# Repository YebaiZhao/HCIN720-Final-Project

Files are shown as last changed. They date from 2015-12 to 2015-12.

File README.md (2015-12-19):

# HCIN720-Final-Project
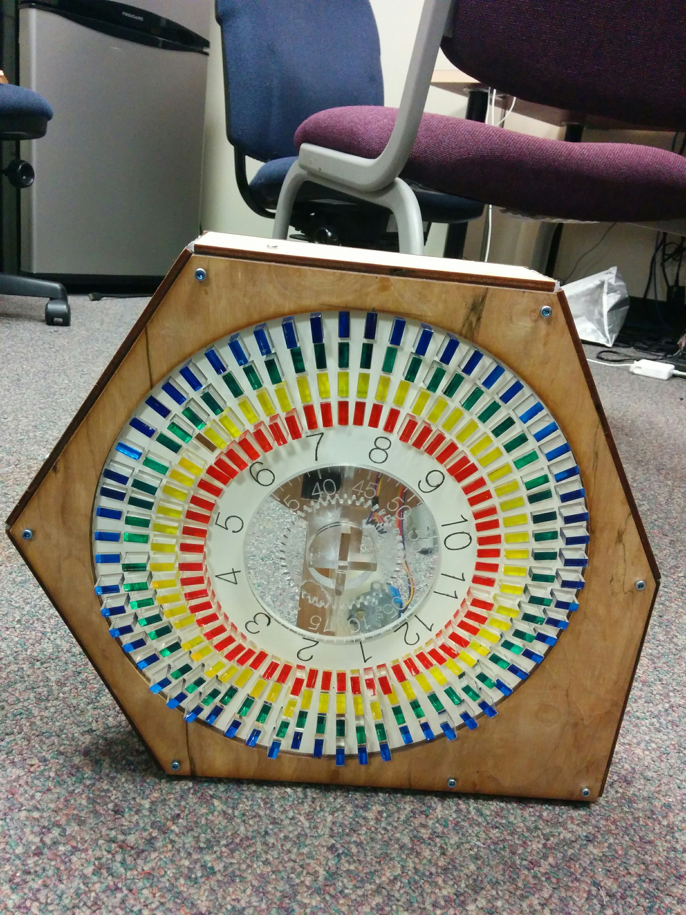
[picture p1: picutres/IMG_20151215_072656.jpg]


A complete prototype including Software for [Photon](https://store.particle.io/), 3D Model, Laser cutting Material for recreating. 

.... is a clock like device for recording the data-- like light temperature and motion, happend around house in 12 hours.

### Docs & Help

- [Software for Photon]() (latest release)
- [3D printing](/3D%20printing%20and%20CAD)
- [laser cutting](/Laser%20Cut)

### 3D printing part

3D printing parts are for holding the minute step motor and hour step motor, which rotate the gears. The .gcode file is avalible [here](/3D%20printing%20and%20CAD/final-motor_holder.gcode) for 3D printing. You could also check the model outlook [here](/3D%20printing%20and%20CAD/final-motor_holder.stl).

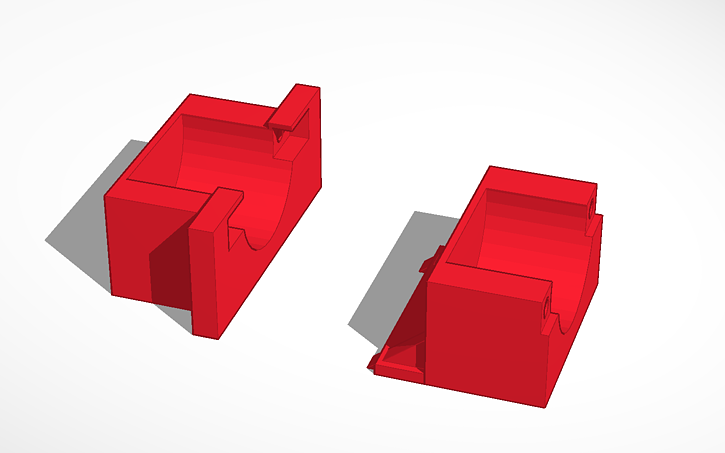
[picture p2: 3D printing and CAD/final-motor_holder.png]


### laser cutting

Laser cutting are serveral part, including, the hour plate, minute plate, gears, acrylic bricks, center support material and the outter box, servo holder. All the parts are avaliable in this [.ai file](/Laser%20Cut/v7.ai) at different layers. The final printing might look like this.

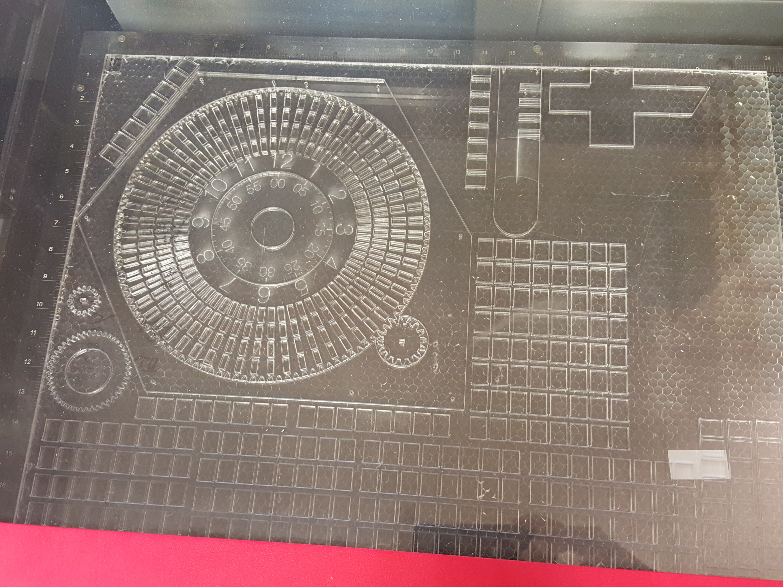
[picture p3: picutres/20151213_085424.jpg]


To customize your own clock, you could paint the hour plate, minute plate and acrylic bricks in different color. We printed the hour plate with white, and acrylic bricks with blue, red, green and yellow, like the first picture.

### Software installation

There are three different files in the software part. The .ino file are avaliable for two photon. [One](/Code/clockOperation.ino) take care of clock operation(including two [step motors](http://www.amazon.com/gp/product/B00JB22IQC?psc=1&redirect=true&ref_=oh_aui_detailpage_o09_s00) and two SG92 servo), and another [one](/Code/sensor.ino) for data collection(here we provide the light sensor and [motion sensor](http://www.amazon.com/gp/product/B013LA6MW0?psc=1&redirect=true&ref_=oh_aui_detailpage_o00_s00) code). Another [.html](/Code/test-version1.html) file is for get temperature data from [weather map API](http://openweathermap.org/api) and send it to photon.

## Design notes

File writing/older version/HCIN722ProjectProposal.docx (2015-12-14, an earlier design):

Project AirDrums

Project Idea and Motivation

Learning to play the drums can be very difficult for some people. They are expensive, with the cost for a complete drum kit ranging from $300-$1000, depending on quality, brand, usage and number of parts. They also require a large space for storage. And last of all, they are loud. Playing the drums can often bother neighbors, or even the residents that live in the same house. As an alternative, there are electronic drums that can solve the noise problem, but, although smaller than the standard drums, they’re hard to carry around.

By building a prototype for a virtual, mobile drum kit, this project aims at enabling its users to carry their “drums” around, wherever they go, requiring only a head-mounted display, some fiducial marker(s) and haptic drum sticks. The use of such a system will not only help aspiring drummers around the world to play and enjoy the music that they love, but also allow individuals to learn and practice, without the complications of purchasing and storing a physical drum kit.

Group Members & Roles

Names | Roles
Anthony Jimenez | Software Programming (good at C#, Python and Java).
Dhananjai Hariharan | Research, System Design, Software Programming (Java, C++, C#. Experience in Android App Development).
Shitao Guo | Software Programming (good at Java, Processing and a little bit C), and soldering if needed.
Tiago Justino | Software Programming (experience with embedded systems and Android. Experience with C, C++, Java, Ruby, Shell)
Ziyan Huang | Software Programming (Java, matlab)

Literature Review

Academic literature demonstrating prior research towards similar goals can be found. Bott et al. [1] proposed a prototype video game for musical expression that used novel 3D spatial interaction techniques using accelerometer based motion controllers, such as the Nintendo Wii Remotes and Nunchuks. The video game provided interfaces for 6 different instruments, each of which used significantly different gestures for playing tunes. Holland et al. [2] introduced the haptic drum kit, which used four computer-controlled vibrotactile devices (controlled by an arduino), attached to the wrists and drums. While that paper introduced the use of haptics towards playing the drums, it still involved a physical drum set while in use.

Other similar research for a more portable and mobile drum set demonstrated a prototype for a portable multi-pitch e-drum with large-area ring shaped pressure sensors. Such a project, while being a work-in-progress, was bendable and robust, as well as succeeded in providing real time sound responses. Smus and Gross [4] presented the ‘Ubiquitous Drums’, a prototype for a wearable drum kit using force sensitive resistors to detect taps and their pressure. It involved placing these sensors on the knees, shoe soles and upper abdominal areas of the user. While it was a work-in-progress demonstration, the downsides of this prototype was that it needed to be connected to a computer using wired connections, since wireless connections resulted in a latency of the sounds being played. Ren et.al [5] developed an interactive virtual percussion instrument system, allowing a group of users to collaboratively emulate music in real time. However, the interactions were limited to a stationary tabletop platform, which also required a large space.

There have also been some attempts at building a virtual reality environment for playing the drums [6]. This implementation uses devices such as the Oculus Rift Head-Mounted display and the Razer Hydra gaming controller. Some shortcomings of such a system were that the user firstly needed to orient himself into the virtual world, then use his real hands control the virtue hands. The whole interaction process made it "hard to play with no resistance", for a lot of users. By enabling users to control they hands directly and visually connect to the world, the level of interaction might give the user more real and natural experience. Combining features from past research, and by using more contemporary devices, it would be possible to develop the proposed mobile haptic drum kit.

Planned Contributions

By developing such a novel method of interaction with virtual instruments in

I meant - this section will say ‘Our project will help improve x y z aspects of HCI in music creation and learning.. I hope you get it. If not, do not worry, I will help you edit it tomorrow morning.

1. provide more ways(interface) to interact with computational music.
2. explore the new dimension of interaction. (not VR, not invisible)
3. test the feasibility and practice of AR interaction for specific purpose ( drum playing ).
4. identify potential issues which might remain in this kind of interaction.

Implementation - Hardware and Software components

Hardware Components:

Google Cardboard kit - x1

Raspberry Pi - x3

IR Camera module - x1

Accelerometer - x2

Vibration motor - x2

USB data cable - x1

Software Components:

Google Cardboard SDK

Android Studio + Android SDK

Unity 3D Game Engine

Raspberry Pi

Operation description:

The depth camera, along with a Raspberry Pi will be attached to the Google Cardboard kit. The camera will be connected to the Pi, which will then perform all the image processing tasks (recognizing gestures/drum hits). The smartphone in the Cardboard will also be connected to the Raspberry Pi, and the Pi will indicate the smartphone what sound to play once the Pi has identified a successful drum hit. These devices working together will emulate AR HMDs like Meta 1 (https://www.spaceglasses.com/).

The haptic drumsticks will act independently by using an accelerometer and a vibration motor (each). Whenever the accelerometer in a stick detects a force that is strong enough, the vibration motors will be triggered, these vibrations will be stronger the as the force detected by the accelerometer increases.

Project Plan (Milestones)

Date | Milestone Description | Team Members
Week 5 (Tue - Feb 24th) | 1. Study google cardboard sdk 2. Study unity sdk | 1. member 1, member 2 2. member 3, member 4
Week 6 (Tue - Mar 3rd) | 1. Run VR hello world on cardboard 2. Run Camera App on cardboard
Week 7 (Tue - Mar 10th) | 1. Implement fiducial mark detection 2. Design / Draw virtual drumset
Week 8 (Tue - Mar 17th) | 1. Configure Pi 2. Connect Kinect to Pi
Week 9 (Tue - Mar 24th) | 1. Run Kinect Hello World 2. Implement gesture recognition with kinect
Week 10 (Tue - Mar 31st) | 1. Track drumstick movement
Week 11 (Tue - Apr 7th) | 1. Design and implement phone - pi synchronization protocol
Week 12 (Tue - Apr 14th) | 1. Detect collision: drumstick vs drums/cymbals (produce audio feedback)
Week 13 (Tue - Apr 21st) | 1. Design and drumstick (vibration motor + accelerometer)
Week 14 (Tue - Apr 28th) | 1. Debug and Evaluation
Week 15 (Tue - May 5th) | 1. Paper writing; 2. Video recording
Week 16 (Tue - May 12th) | Final Delivery | -

Project Goal

References

[1] Jared N. Bott, James G. Crowley, Joseph J. LaViola Jr. “Exploring 3D Gestural Interfaces for Music Creation in Video Games”. FDG ‘09 Proceedings of the 4th International Conference on Foundations of Digital Games. DOI: http://dx.doi.org.ezproxy.rit.edu/10.1145/1536513.1536527

[2] Simon Holland, Anders J. Bouwer, Mathew Dalgleish, Topi M. Hurtig. “Feeling the Beat Where it Counts: Fostering Multi-Limb Rhythm Skills with the Haptic Drum Kit”. TEI ‘10 Proceedings of the fourth international conference on Tangible, embedded, and embodied interaction. DOI: http://dx.doi.org/10.1145/1709886.1709892

[3] Chun-Ming Lo, Tsung-Ching Huang, Cheng-Yi Chiang, Johnson Hou, Kwang-Ting Cheng. “A portable Multi-pitch e-drum based on printed flexible pressure sensors”. DATE '10 Proceedings of the Conference on Design, Automation and Test in Europe.

[4] Boris Smus, Mark D. Gross. “Ubiquitous Drums: a Tangible, Wearable Musical Interface”. CHI EA 2010. DOI: http://dx.doi.org/10.1145/1753846.1754094

[5] Zhimin Ren, Ravish Mehra, Jason Coposky, Ming C. Lin. “Tabletop Ensemble: touch enabled virtual percussion instruments”. I3D ‘12 Proceedings of the ACM SIGGRAPH Symposium on Interactive 3D Graphics and Games. DOI: http://dx.doi.org/10.1145/2159616.2159618

[6] Drums with Oculus Rift and Razer Hydra (Video): http://vimeo.com/66023452

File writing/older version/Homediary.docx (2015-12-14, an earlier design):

Define and describe your problem. What kind of problem do you want to solve? Keep it simple and solvable; rather than “solve world hunger,” you might try “sandwich making robot.” It should involve an Internet-connected device.

Do a literature search in the HCI conferences (CHI, UIST, Ubicomp, ISWC, and so on) and summarize how other people have approached this or similar problems. Also look at various IoT objects at iotlist.co and other places.

Describe your proposed solution.

Outline the steps you will take to implement your solution.

Problem Definition

With the development of modern computer technology, people nowadays have unprecedented number of choices to gather the information created by the actions inside or around their houses, such as video recording, motion detecting, temperature or sound monitoring. While many smart home monitoring systems are able to record and store the data under time sequence, most of them keep the data separately. This makes people in the house less likely to review the data, since it consumes much time and effort. Smart video cameras can store the surveillance video continuously, but people might not willing to watch the content, and research also indicates that people might feel uncomfortable to have all their movement at home recorded. If users purely want to know whether their family members or pets were at home at a certain time, motion sensors might more favorable than cameras.

Other types of information, such as the sound, light, temperature or power consumption of a house, are rarely tracked based on the time. Although they are less expressive than the video footage, combining and comparing different types of data might be enlightening and interesting to common people, as that can be seen as the life log of the house. However, it is hard to find an implementation that successfully visualized those data in common houses. It can be intriguing if a device can blend in the household environment and visualize information from multiple source in the house in an artistic way.

Motion detectors can be used not only as a way to detect intruders of the house, it can also used to track the movement status of the residents. As we known that sitting in front of the computer or TV are usually not healthy for people, it is possible that motion detectors can track residents’ motion in the room and notify them when they have sat too long.

Related research

Combining different sensors in surveillance has become an evolving research area [2]. Johns Hopkins provided a method to design such multimedia surveillance system, which addressed the problem related to deployment of multiple sensors [3]. Efforts were also made to address the issue about coordination of multiple video camera. However, less researches explore dimensions of the representation of surveillance data around the house. Eun Kyoung Choe and Sunny Consolvo, demonstrated that people would not want to be recorded at home through an anonymous survey. This indicates the importance of the use of sensors and the approach of data visualization.

On the other hand, periodical data is also presented in various physical forms. The studio NAND has presented EMOTO, which use 3D physical data sculpture to visualize the global response around the London 2012 Olympic Games on Twitter. In other work, Laurie Frick demonstrates her daily activities and nightly sleep data with 2D ink and watercolor drawing. And the Physical Visualization website [http://dataphys.org/list/] also shows a list of physical data visualization examples.

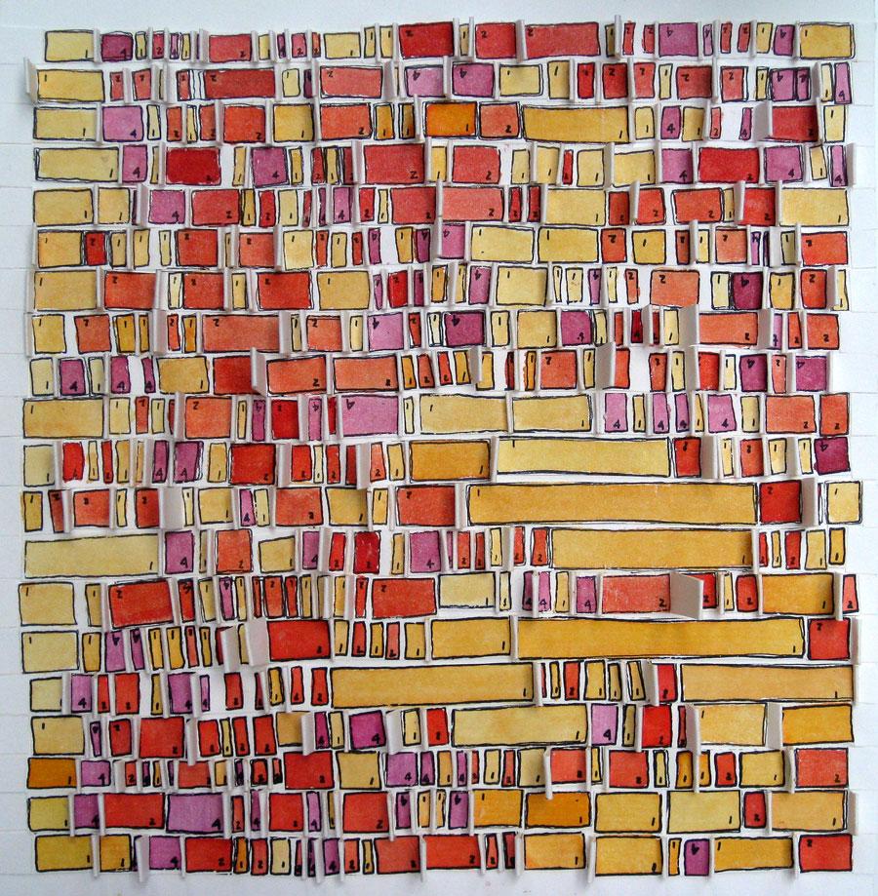
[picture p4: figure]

Laurie Frick's Pokey Red is a physical visualization of sleep data over a month

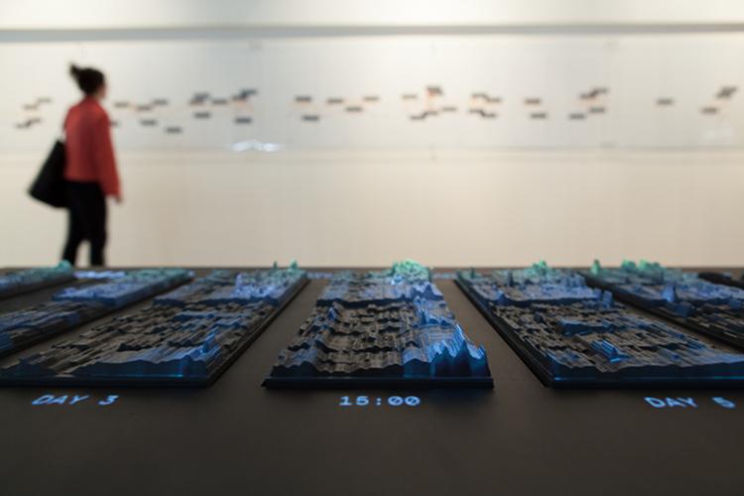
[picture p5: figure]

2012 – Emoto: Visualizing the global response at the

London 2012 Olympic Games on Twitter.

On the whole, we realize that discussion related home surveillance system less focused on the expressions of its data, which however have rise a reasonable research interest.

Proposed solution

Our group believes that based on what we have learned in this course, it is possible to build a system which collects one or several types of data from sensors, then records and presents the data with a less intrusive output. We think users can benefit from looking at this output to learn more about what has happened recently. As pet owners can check how was their pet doing along at home; tenants can check how the public space and utilities are used; families can share more detailed information with each other and know deeper about the house. Since the data is transmitted through the internet, when the sensors separate from the output, users might able to see the status of their house or share it with other people.

Implementation

We are thinking about using several internet-enabled micro-controllers with sensors to monitor the house and send the data to a central micro-controller which controls the output system. The output system is in charge of visualizing the data under timely order. As we are inspired by the electrocardiograph device, our current design it to build the output system with several colored pens controlled individually moving on a roll of paper or a plate of paper. Other materials will be considered if possible. If pen heads are moving in a circular motion, it might be also used as a wall clock, which the hour hand is drawn on the paper with colors. But this will require users to change the clock face paper each 12 hours after on circle is completed. Otherwise, if the paper is going from one roll to another, the drawing can be kept longer than a day.

We are still discussing and finding a better way of implementing our concept, more interaction might be added if time permits.

Reference

1. Choe, E. K., Consolvo, S., Jung, J., Harrison, B., & Kientz, J. A. (2011). Living in a Glass House: A Survey of Private Moments in the Home. In Proceedings of the 13th International Conference on Ubiquitous Computing (pp. 41–44). New York, NY, USA: ACM. http://doi.org/10.1145/2030112.2030118
2. Luo, R. C., Yih, C.-C., & Su, K. L. (2002). Multisensor fusion and integration: approaches, applications, and future research directions. IEEE Sensors Journal, 2(2), 107–119. http://doi.org/10.1109/JSEN.2002.1000251
3. Sivaram, G. S. V. S., Kankanhalli, M. S., & Ramakrishnan, K. R. (2009). Design of Multimedia Surveillance Systems. ACM Trans. Multimedia Comput. Commun. Appl., 5(3), 23:1–23:25. http://doi.org/10.1145/1556134.1556140

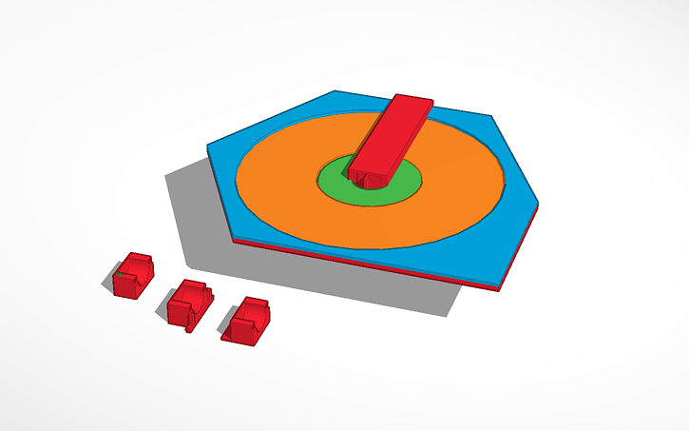
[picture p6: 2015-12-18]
3D printing and CAD/final-clock_overview.png

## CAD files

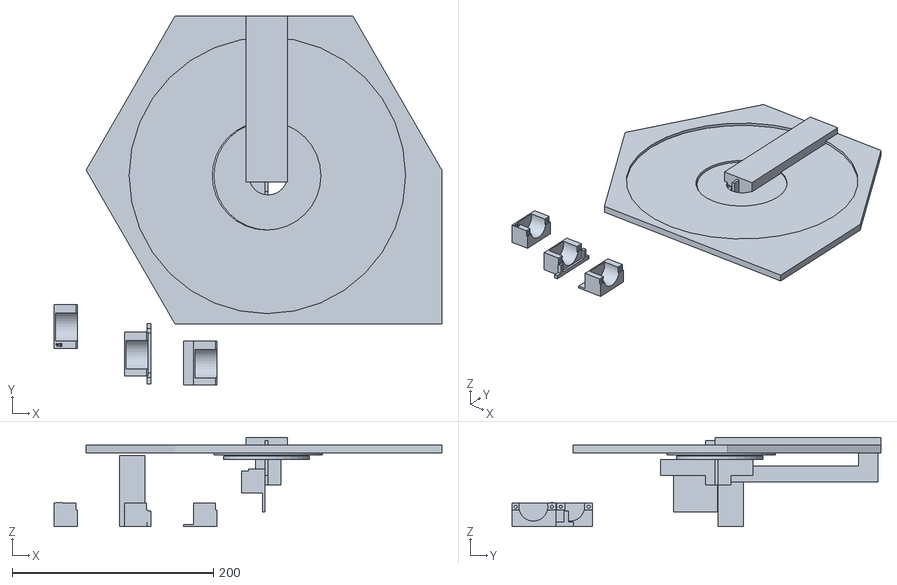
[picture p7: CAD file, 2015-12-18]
3D printing and CAD/final-clock_overview.stl
385.3 x 366.7 x 88.9

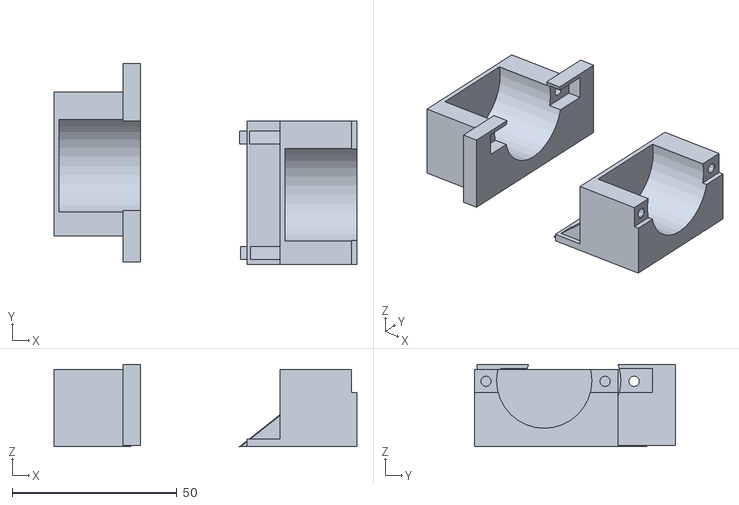
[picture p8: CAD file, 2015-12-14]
3D printing and CAD/final-motor_holder.stl
91.9 x 61.1 x 25.0

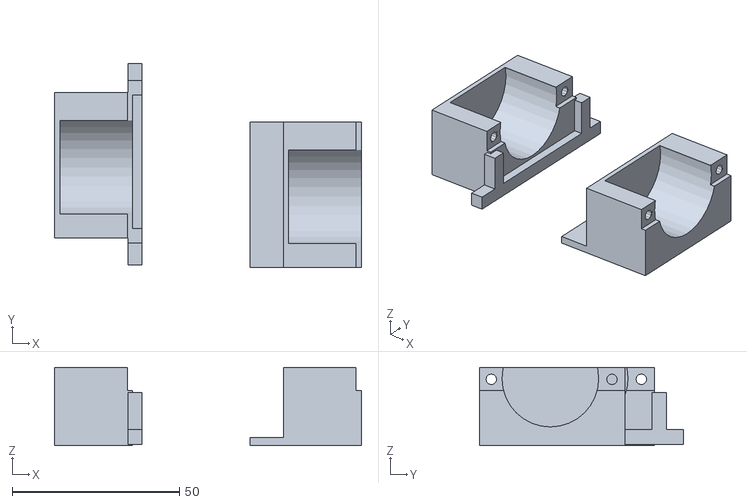
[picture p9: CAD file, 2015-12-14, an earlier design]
3D printing and CAD/older version/finial.stl
91.9 x 61.1 x 23.4

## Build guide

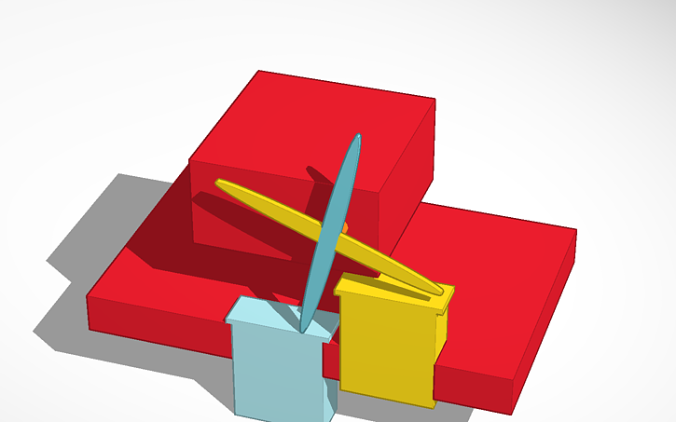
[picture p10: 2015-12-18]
3D printing and CAD/proving_brick_movement.png

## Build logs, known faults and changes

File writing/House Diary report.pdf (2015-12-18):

# House Diary: a Digital Home Data Monitoring and Visualization System

Problem Definition
With the development of modern computer technology, people nowadays have unprecedented number of choices to gather the information created by the actions inside or around their houses, such as video recording, motion detecting, temperature or sound monitoring. While many smart home monitoring systems are able to record and store the data under time sequence, most of them keep the data separately. This makes people in the house less likely to review the data, since it consumes much time and effort. Smart video cameras can store the surveillance video continuously, but people might not willing to watch the content, and research also indicates that people might feel uncomfortable to have all their movement at home recorded. If users purely want to know whether their family members or pets were at home at a certain time, motion sensors might more favorable than cameras.

Other types of information, such as the sound, light, temperature or power consumption of a house, are rarely tracked based on the time. Although they are less expressive than the video footage, combining and comparing different types of data might be enlightening and interesting to common people, as that can be seen as the life log of the house. However, it is hard to find an implementation that successfully visualized those data in common houses. It can be intriguing if a device can blend in the household environment and visualize information from multiple source in the house in an artistic way.

Motion detectors can be used not only as a way to detect intruders of the house, it can also be used to track the movement status of the residents. As we known that sitting in front of the computer or TV are usually not healthy for people, it is possible that motion detectors can track residents’ motion in the room and notify them when they have sat too long.

Related research

Ziyan Huang
Rochester Institute of
Technology, NY
zh9842@g.rit.edu

Yebai Zhao
Rochester Institute of
Technology, NY
Yz9422@g.rit.edu

Combining different sensors in surveillance has become an evolving research area [2]. Johns Hopkins provided a method to design such multimedia surveillance system, which addressed the problem related to deployment of multiple sensors [3]. Efforts were also made to address the issue about coordination of multiple video camera. However, less researches explore dimensions of the representation of surveillance data around the house. Eun Kyoung Choe and Sunny Consolvo, demonstrated that people would not want to be recorded at home through an anonymous survey. This indicates the importance of the use of sensors and the approach of data visualization.

Except the purpose of home surveillance, there are other reasons for deploying sensors around the house. Research study around home system is another reason. Jennifer Beaudin and Stephen Intille described the problems and solution they found when using ubiquitous sensors for data collection in real homes [4]. Their core kit contained a thin wire reed switch, a magnet and a storage board with coin battery, which was fixed with physically manipulated object around house to record the actions. Additionally, they also included infrared beacons on the ceiling to detect the position of the user who wear a receiver. This paper defined problems around such tool kit for study purpose, such as the visibility, attachability, the installation and so on.

Self-reflection is another important issue around the activity tracking topic. This issue of how technology should be designed to support people’s reflection has been raised and discussed [5]. Most of reflection and awareness technology in HCI have been focused on affective system, which reflect the emotion and feeling, such as EmoteMail [6], affective diary [7], or Affector [8]. There are also discussion and researches related to reflection of body physiology, movement and behaviors. For example, Enhancing Self-Reflection with Wearable Sensors [9], Personal Informatics in the Wild: Hacking Habits for Health & Happiness [10], And Footprint Tracker [11]. However rare research mentioned the reflection about the house. Combining the surveillance system and data visualization to contribute the reflection of our home, could be an interesting and valuable topic.

We are considering visualizing the home data in physical form. There are various physical forms presenting periodical data to emphasize the reflection. The studio NAND has presented EMOTO, which use 3D physical data sculpture to visualize the global response around the London 2012 Olympic Games on Twitter [Figure 2]. In other work, Laurie Frick demonstrates her daily activities and nightly sleep data with 2D ink and watercolor drawing [Figure 1]. And the Physical Visualization website [http://dataphys.org/list/] also shows a list of physical data visualization examples.

On the whole, we realize that discussion related home surveillance system less focused on the expressions of its data, which however have rise a reasonable research interest.

Proposed solution

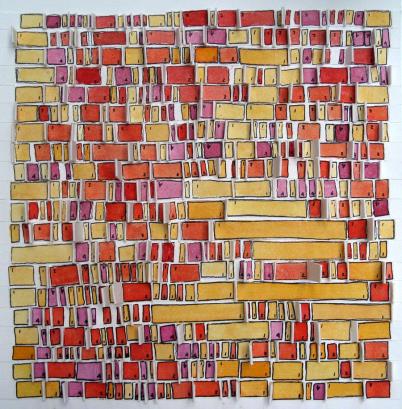
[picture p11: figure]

Figure 1. Laurie Frick's Pokey Red is a physical visualization of sleep data over a month

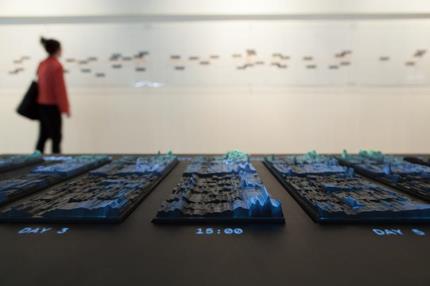
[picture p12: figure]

Figure 2. Emoto: Visualizing the global response at the London 2012 Olympic Games on Twitter

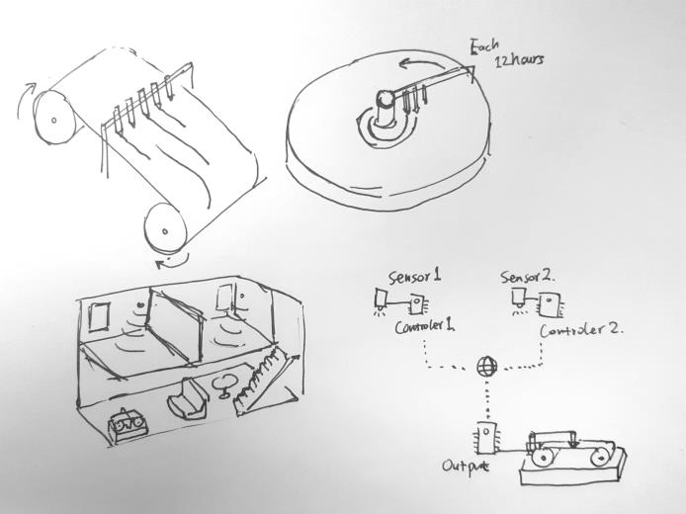
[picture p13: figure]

Our group believes that based on what we have learned in this course, it is possible to build a system which collects one or several types of data from sensors, then records and presents the data with a less intrusive output. We think users can benefit from looking at this output to learn more about what has happened recently. As pet owners can check how was their pet doing along at home; tenants can check how the public space and utilities are used; families can share more detailed information with each other and know deeper about the house. Since the data is transmitted through the internet, when the sensors separate from the output, users might able to see the status of their house or share it with other people.

Proposed Implementation
As Figure 3 shows, we are thinking about using several internet-enabled micro-controllers with sensors to monitor the house and send the data to a central micro-controller which controls the output system. The output system is in charge of visualizing the data under timely order. As we are inspired by the electrocardiograph device, our current design it to build the output system with several colored pens controlled individually moving on a roll of paper or a plate of paper. Other materials will be considered if possible. If pen heads are moving in a circular motion, it might be also used as a wall clock, which the hour hand is drawn on the paper with colors. But this will require users to change the clock face paper each 12 hours after on circle is completed. Otherwise, if the paper is going from one roll to another, the drawing can be kept longer than a day.

Currently, we are going to attach micro solenoids to a 3D printed arm which controls the movement of color pens. A set of gears will be set for moving either this arm or the paper base under a timed order. Based on our last project, the motor and the control board are capable of providing strong torque in a very low speed. We also have gained experience on controlling multiple magnets with integrated circuit. The basic moving mechanism can be either close to the Linear Clock (http://www.instructables.com/id/Linear-Clock/) or the Arduino clock v.2.0. (http://www.instructables.com/id/Arduino-clock-v20/) We will determine the best implementation based on our project’s need. Since this system is designed to work indoor at home, it should be better working with Wi-Fi enabled microcontroller. We plan to keep using Particle Photon because it is small and we have learned a lot about how to develop program on this platform. The data collection will be accomplished with a sensor such like the PIR Motion Sensor (https://www.sparkfun.com/products/13285) for sparkfun.com, a Photon, a power source

Figure 3. The design of the system (below) and the drawing output (above)

such like a Lithium Ion Battery and some serve circut. Using the cloud service, the Photon in the output system can easily subscribe multiple information source from other Photons.

We are still discussing and finding a better way of implementing our concept, more interaction might be added if time permits.

Project progress
Initial Solution
Our group believes that based on what we have learned in this course, it is possible to build a system which collects one or several types of data from sensors, then records and presents the data with a less intrusive output. We think users can benefit from looking at this output to learn more about what has happened recently. For example, pet owners can check how was their pet doing along at home; tenants can check how the public space and utilities are used; families can share more detailed information with each other and know deeper about the house. Since the data is transmitted through the internet, when the sensors separate from the output, users might able to see the status of their house or share it with other people.

Design
We spent many time on discussing the possible ways to implement our initial concept. Although using pen+paper might be an easy answer, this solution has two significant drawbacks: user have to change the consumable writing material, both paper and the ink; and it is hard to incorporate with on-the market pens with our motors and gears, which might lead to an unstable physical system.

Thus, we started to consider self-erasable material, such like sand or plasticine. To fulfill our system design requirement, multiple data source should be able to be visualized with quantitative representation. A sandbox will not have the accuracy we need, unless it is very big and have many different kinds of sand. We did a simple test on the plasticine idea with some Play-Doh.We found that it might require high pressure and complicated settings to use mechanical method to erase the mark on plasticine. Softer plasticine material can dry out within several days, because they use water as the dispersant. However, the oil-based plasticine is harder in texture.

In the end, we decide to use acrylic bricks as the information indicator. To connect the time will the data, the acrylic bricks will be mounted on a clock surface, and the entire output device will be able to work like a clock.

Implementation
Software:
There are three sections in software Part of project implementation - clock basic operation, push acrylic according received data, data source. The first segment to implement clock basic operation. Instead of making two step motor move continuously for 24 hours, we are pushing it to move specific angle periodically -- hour plate moves 6 degrees every 12 minutes, and minute plate move 6 degrees every minute. There are two main reasons for this change. First is to avoid the error in calculation of moving speed of step motor (step motor is more accurate in move specific angle). The second reason is to corporate with the movement of acrylic. Since we control the servo to push acrylic brick in the vertical direction of hour plate, to decrease the fraction between movement of hour plate and movable acrylic, the hour plate need to stop when servo push the movable acrylic. Another important aspect of clock operation is the steps number for step motor each time. In order to lower error of angle, that step motor run each time, the motor need to move integer steps. Since we are using the 4096 step motor, which means a full circle takes 4096 step, this condition also constrains the number of gears (calculation seeing below). Considering we are both running minute plate and hour plate, as mentioned before, every 12 minutes the minute plate and hour plate will run at the same time. To achieve this, multiple threads are applied in this case. One thread is for the minute plate moving, another thread is for the hour plate and servo running.

In the second segments, sensors send data to the main Photon (which run step motors and servos) every 30 second. Photon will calculate the average of data in 12 minute, and push the servo to move the acrylic brick after step motor finish turning. To augment the visualization of data, the height of movable acrylic (which is controlled by the servo) need to fit to the range of data. For example, the temperature data which got from the web, only set to the range of usual temperature. There is another hardware issue comes with running two servos with photon. Since the voltage provided by the photon is not enough to support two servos, we tried to run it with additional 5-volt battery. However, the outcome is unstable. To define the problem, we tested signal to serve with an oscilloscope. It is shown the noise in the signal, which come with the battery. Instead of using extra battery, we used the USB to get the power source.

For the data source, for now we are using light sensors, motion detector (from Amazon: http://www.amazon.com/gp/product/B013LA6MW0?psc=1&redirect=true&ref_=oh_aui_detailpage_o00_s00) and temperature data from the web (http://openweathermap.org/api). Due to the needs of time adjustment, every time flashes the code into a photon, user need to reset the clock from the serial port

Hardware
To make the clock, we built our design on the Illustrator file for the laser cutter. In last project we noticed that the print time of the 3D printer is too long that it might slow down the prototyping process. So in this project we are more willing to use the laser cutter to make the parts we need. If the size of certain part needs adjustment, we can do it easily on the laser cutter Illustrator file. After the cutting file was made, we made a wooden model for the proof of concept (Figure 5). Since we want to save the expensive acrylic board we brought, the acrylic was not used until most of the parts have been proved to be in the right size. During the testing, we want the acrylic brick and the hole fit as close as possible, maintaining a smooth but also tight movement. In order to achieve that, we cut holes with tiny difference on the length and width (Figure 7). After this test I was able to draw the design file with just right amount of space for the servos to push the bricks (Figure 4, 6).

We found a website called “Gear Generator” to make the gear pattern we need in this project. After we learned about the step motor’s behavior, we calculated that the bigger gear plate for minute and hour display should have 15*n teeth, and the smaller gear on the motor should have 2n number of teeth. This will keep the rotating plate stop every 6 degrees with no error. (For each minute, the minute plate should turn 6 degrees.)

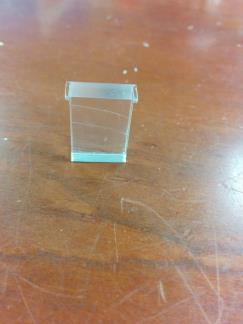
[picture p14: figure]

Figure 4. The acrylic brick

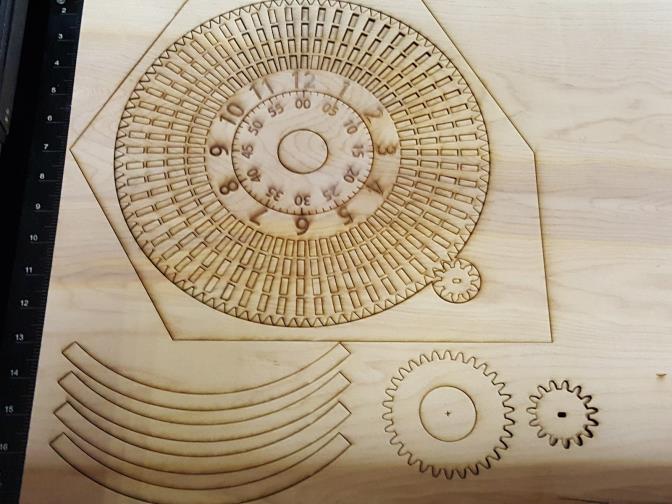
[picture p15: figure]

Figure 5. The wooden test

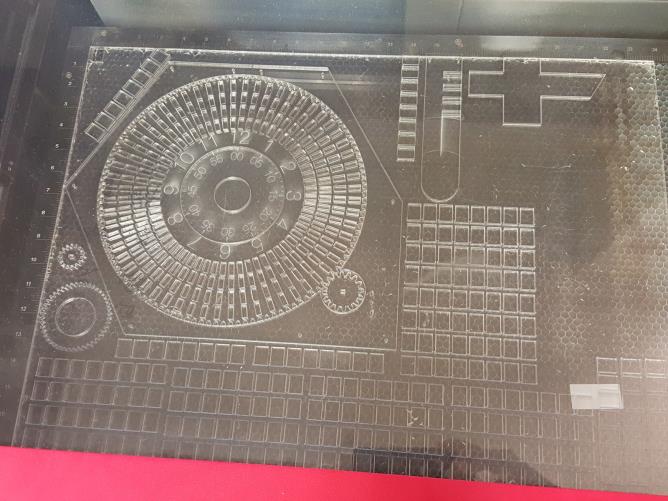
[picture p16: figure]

Figure 6. The finial acrylic board

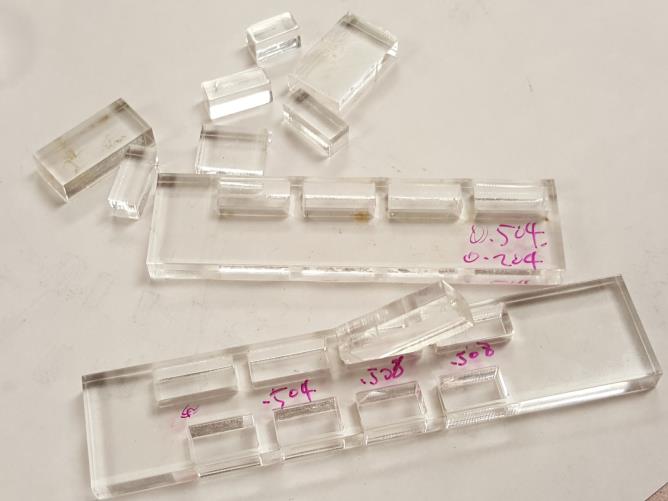
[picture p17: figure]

Figure 7. Test for the cutting width

In the assembly, we used many glue instead of screws and bolts. This saved us some efforts in the design process, but once the glue is cured, we won’t be able to do any adjustment.

The finial result is a half-success, since in the design there should be damping grease to work as the support, lubrication and stick the brick in the position until being pushed. But we didn’t able to find the right damping grease in time neither online nor locally. We believe that if we have the grease, this output device will able to work properly.

Lesson Learned and discussion
If we have more acrylic and wood board for the testing, we might able to make the test easier. Because we can make the prototype one at a time.

While doing a hardware + software combined debugging, oscilloscope is a wonderful tool to see whether the problem is coming from the software or the hardware. It also can help us identify what can be the possible problem through the signal transmitting.

For software part, self-adaptive data might be an important functionality to consider in future implementation. For example, the temperature data have different range between summer and winter. If we choose a large range to contain temperature both in summer and winter, the visualization of daily temperature change might not be obvious. It is better for device to change the temperature range periodically based on recent records.

It’s also interesting to know, how users will understand and translate data from this clock. For example, how many information might be the maximum for user to perceive? Which data representation most user would prefer, adaptive or fixed? How user will combine different data together to reflect their house status? All the question will influence the design to better fit users need.

References
1. Choe, E. K., Consolvo, S., Jung, J., Harrison, B., & Kientz, J. A. (2011). Living in a Glass House: A Survey of Private Moments in the Home. In Proceedings of the 13th International Conference on Ubiquitous Computing (pp. 41–44). New York, NY, USA: ACM.
http://doi.org/10.1145/2030112.2030118
2. Luo, R. C., Yih, C.-C., & Su, K. L. (2002). Multisensor fusion and integration: approaches, applications, and future research directions. IEEE Sensors Journal, 2(2), 107–119. http://doi.org/10.1109/JSEN.2002.1000251
3. Sivaram, G. S. V. S., Kankanhalli, M. S., & Ramakrishnan, K. R. (2009). Design of Multimedia Surveillance Systems. ACM Trans. Multimedia Comput. Commun. Appl., 5(3), 23:1–23:25. http://doi.org/10.1145/1556134.1556140
4. Beaudin, J., Intille, S., & Tapia, E. M. (2004). Lessons Learned Using Ubiquitous Sensors for Data Collection in Real Homes. In CHI ’04 Extended Abstracts on Human Factors in Computing Systems (pp. 1359–1362). New York, NY, USA: ACM.http://doi.org/10.1145/985921.986064
5. Sas, C., & Dix, A. (2009). Designing for Reflection on Experience. In CHI ’09 Extended Abstracts on Human Factors in Computing Systems (pp. 4741– 4744). New York, NY, USA:
ACM.http://doi.org/10.1145/1520340.1520730

6. Ängeslevä, J., Reynolds, C., & O’Modhrain, S. (2004). EmoteMail. In ACM SIGGRAPH 2004 Posters (p. 9–). New York, NY, USA: ACM.http://doi.org/10.1145/1186415.1186426
7. Lindström, M., St\a ahl, A., Höök, K., Sundström, P., Laaksolathi, J., Combetto, M., … Bresin, R. (2006). Affective Diary: Designing for Bodily Expressiveness and Self-reflection. In CHI ’06 Extended Abstracts on Human Factors in Computing Systems (pp. 1037–1042). New York, NY, USA:
ACM.http://doi.org/10.1145/1125451.1125649
8. Boehner, K., DePaula, R., Dourish, P., & Sengers,
P. (2005). Affect: From Information to Interaction. In Proceedings of the 4th Decennial Conference on Critical Computing: Between Sense and Sensibility (pp. 59–68). New York, NY, USA: ACM.http://doi.org/10.1145/1094562.1094570
9. Kefalidou, G., Skatova, A., Brown, M., Shipp, V., Pinchin, J., Kelly, P., … Sun, X. (2014). Enhancing Self-reflection with Wearable Sensors. In Proceedings of the 16th International Conference on Human-computer Interaction with Mobile Devices & Services (pp. 577–580). New York, NY, USA:
ACM.http://doi.org/10.1145/2628363.2634257
10. Li, I., Froehlich, J., Larsen, J. E., Grevet, C., & Ramirez, E. (2013). Personal Informatics in the Wild: Hacking Habits for Health & Happiness. In CHI ’13 Extended Abstracts on Human Factors in Computing Systems (pp. 3179–3182). New York, NY, USA:
ACM.http://doi.org/10.1145/2468356.2479641
11. Gouveia, R., & Karapanos, E. (2013). Footprint Tracker: Supporting Diary Studies with Lifelogging. In Proceedings of the SIGCHI Conference on Human Factors in Computing Systems (pp. 2921– 2930). New York, NY, USA:
ACM.http://doi.org/10.1145/2470654.2481405

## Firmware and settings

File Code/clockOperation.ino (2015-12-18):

#include "application.h"
#include <stdio.h>
#include <stdlib.h>


/////////////////////////////////////////// The setting for Servo /////////////////////////////////////////////////
Servo myservo1;
Servo myservo2;
//unsigned long lastTime = 0UL;
char x[256];
int pos1 = 90;    // variable to store the servo position
int pos2 = 90;    // variable to store the servo position
int change1 = D0;
int change2 = D1;

//For lightdata
//int i = 0;
int lightData;
int lightDataNum = 0;
int lightTotal = 0;
int lightAve = 0;
int LIGHT_MIN = 0;
int LIGHT_RANGE = 1000;

//For webTemp data
int webTemp;
int webTempNum = 0;
int webTempTotal = 0;
int webTempAvg = 0;
int TEMP_MIN = 30;
int TEMP_RANGE = 50;

//For motion data
int ifMotion;
int ifMotionNum = 0;
int ifMotionTotal = 0;
int ifMotionAvg = 0;
int MOTION_MIN = 0;
int MOTION_RANGE = 10;

//The parameter for original state
int ORIGIN_POS = 90;
//The parameter for the range of servo
int SERVO_LARGE = 80;
int SERVO_MIN = 10;
//The parameter for the range of each source
//4096 for a circle
int STEPFORCIRCLE = 4096;


/////////////////////////////////////////// The setting for motor /////////////////////////////////////////////////


///////////////////////////Set the gears number//////////////////////////////
//requirement: (HOUR_LGEARNUM/HOUR_SGEARNUM)*HOUR_DEGREE = 45*n
//number of gears in large wheel
int HOUR_LGEARNUM = 120;
//number of gears in small wheel
int HOUR_SGEARNUM = 16;
//number of seperation for every 30 degree
double HOUR_DEGREE = 6; //need to with 6 degree
//requirement: (MIN_LGEARNUM/MIN_SGEARNUM)*MIN_DEGREE = 45*n
int MIN_LGEARNUM = 45;
int MIN_SGEARNUM = 16;
double MIN_DEGREE = 6;


/////////////////////////////// Set the pin //////////////////////////////////
int HOUR_MOTOR1 = A0;
int HOUR_MOTOR2 = A1;
int HOUR_MOTOR3 = A2;
int HOUR_MOTOR4 = A3;
int MIN_MOTOR1 = D2;
int MIN_MOTOR2 = D3;
int MIN_MOTOR3 = D4;
int MIN_MOTOR4 = D5;


/////////// Change the time interval &&& Moving steps each time ///////////////

//12 minute, 120000*HOUR_DEGREE
unsigned long Hour_Time_Interval = 20000UL;
//5 minute, (related to MIN_DEGREE, 6 = 1min)
unsigned long Min_Time_Interval = 20000UL;
//步进电机转一圈8秒
// int StepForHour = -moveSteps(HOUR_DEGREE, HOUR_LGEARNUM, HOUR_SGEARNUM);
// int StepForMin = moveSteps(MIN_DEGREE, MIN_LGEARNUM, MIN_SGEARNUM);
//for testing
// int StepForHour = -4096;
// int StepForMin = 4096;
int StepForHour = (-1)*(STEPFORCIRCLE*HOUR_DEGREE*(HOUR_LGEARNUM/HOUR_SGEARNUM)/360);
int StepForMin = STEPFORCIRCLE*MIN_DEGREE*(MIN_LGEARNUM/MIN_SGEARNUM)/360;

int moveSteps(double LmoveDegree, int LGs, int SGs)
{
    //how many degree for small gears, for one move of big gear
    int moveSteps = STEPFORCIRCLE*LmoveDegree*(LGs/SGs)/360;
    //need to have factor of 3*3*5
    //how many steps needed for those degree
    // int moveSteps = STEPFORCIRCLE*SmoveDegree/360;
    //in order to make moveSteps to int, (l/s)(degreeEach), need to have factor of 3*3*5
    return moveSteps;
}

/////////////////////////////////////////////// Threads Setting //////////////////////////////////////////////////

////////////////////Thread parameter structure &&&&& Set the parameter/////////////////
typedef struct {
    int motor1;
    int motor2;
    int motor3;
    int motor4;
    int steps;
    unsigned long duration;
    unsigned long lastTime;
    unsigned long now;
} MOTOR_PARAM;

// Defines thread parameters
MOTOR_PARAM motor1Param = {HOUR_MOTOR1, HOUR_MOTOR2, HOUR_MOTOR3, HOUR_MOTOR4, StepForHour, Hour_Time_Interval, 0UL, 0UL};

MOTOR_PARAM motor2Param = {MIN_MOTOR1, MIN_MOTOR2, MIN_MOTOR3, MIN_MOTOR4, StepForMin, Min_Time_Interval, 0UL, 0UL};


/////////////////// Define the thread &&& Give Function of Thread ///////////////////
Thread* motor1Thread;
Thread* motor2Thread;

os_thread_return_t motor2MOVE(void* param){
    MOTOR_PARAM *p = (MOTOR_PARAM*)param;

    // Start never ending loop
    for(;;) {

        p->now = millis();
        //digitalWrite(p->pin, LOW);
        //Serial.print(p->now - p->lastTime);
        //Serial.print(p->lastTime);
        if ((p->now)-(p->lastTime)>(p->duration)) {
            Serial.print("run");
            p->lastTime = p->now;
            move(p->steps, p->motor1, p->motor2, p->motor3, p->motor4);
        }
    }
}

os_thread_return_t motor1MOVE(void* param){
    MOTOR_PARAM *p = (MOTOR_PARAM*)param;

    // Start never ending loop
    for(;;) {
        p->now = millis();
        //digitalWrite(p->pin, LOW);
        //Serial.print(p->now - p->lastTime);
        //Serial.print(p->lastTime);
        if ((p->now)-(p->lastTime)>(p->duration)) {
            Serial.print("run");

            // run step motor
            p->lastTime = p->now;
            move(p->steps, p->motor1, p->motor2, p->motor3, p->motor4);

            // run
            //For light Sensor
            Serial.print("movelightFrom: ");
            Serial.print(ORIGIN_POS);
            Serial.print(", lightAverageData");
            Serial.print(lightAve);
            pos1 = ORIGIN_POS + lightAve*(SERVO_LARGE-SERVO_MIN)/LIGHT_RANGE + SERVO_MIN;
            myservo1.write(pos1);
            Serial.print(", to: ");
            Serial.println(pos1);

            delay(1000);
            //push down
            pos1 = ORIGIN_POS;
            myservo1.write(pos1);
            Serial.print("back");
            Serial.println(pos1);
            delay(1000);

            //for the web data
            // Serial.print("TempMoveFrom: ");
            // Serial.print(ORIGIN_POS);
            // Serial.print(", tempAverageData");
            // Serial.print(webTempAvg);
            pos1 = ORIGIN_POS - webTempAvg*(SERVO_LARGE-SERVO_MIN)/TEMP_RANGE - SERVO_MIN;
            myservo1.write(pos1);
            // Serial.print(", to: ");
            // Serial.println(pos1);

            delay(1000);
            //push down
            pos1 = ORIGIN_POS;
            myservo1.write(pos1);
            // Serial.print("back");
            // Serial.println(pos1);
            delay(1000);
            //for Motion data
            // Serial.print("moveMotionFrom: ");
            // Serial.print(ORIGIN_POS);
            // Serial.print(", MotionAverageData");
            // Serial.print(ifMotionAvg);
            pos2 = ORIGIN_POS - ifMotionAvg*(SERVO_LARGE-SERVO_MIN)/MOTION_RANGE - SERVO_MIN;
            myservo2.write(pos2);
            // Serial.print(", to: ");
            // Serial.println(pos2);

            delay(1000);
            //push down
            pos2 = ORIGIN_POS;
            myservo2.write(pos2);
            // Serial.print("back");
            // Serial.println(pos2);


            ifMotionNum = 0;
            ifMotionTotal = 0;
            webTempNum = 0;
            webTempTotal = 0;
            lightDataNum = 0;
            lightTotal = 0;
        }
    }
}




/////////////////////////////////////////////////// Begin to Run ///////////////////////////////////////////////////////
void setup() {

    Serial.begin(9600);
    Serial.println("Let's begin!");



    //Set pin mode
    pinMode(change1, OUTPUT);
    pinMode(change2, OUTPUT);
    pinMode(HOUR_MOTOR1, OUTPUT);
    pinMode(HOUR_MOTOR2, OUTPUT);
    pinMode(HOUR_MOTOR3, OUTPUT);
    pinMode(HOUR_MOTOR4, OUTPUT);
    pinMode(MIN_MOTOR1, OUTPUT);
    pinMode(MIN_MOTOR2, OUTPUT);
    pinMode(MIN_MOTOR3, OUTPUT);
    pinMode(MIN_MOTOR4, OUTPUT);

    //set the servo
    myservo1.attach(change1);
    myservo2.attach(change2);

    //set internet
    Particle.subscribe("light1991pwpw", lightHandler, "2f0038000547343339373536");
    Particle.subscribe("motion", motionHandler, "2f0038000547343339373536");
    Spark.function("temp",tempChange);

}

//setting for adjust
double hour_small_degree = 0.5;
int hour_large_degree = 6;
double minute_small_degree = 0.5;
int minute_large_degree = 6;
// int HOUR_LGEARNUM = 120;
// int HOUR_SGEARNUM = 16;
// int HOUR_DEGREE = 6;
// int MIN_LGEARNUM = 45;
// int MIN_SGEARNUM = 16;
// int MIN_DEGREE = 6;


void loop() {
    // Nothing here.
    //moveSteps(double LmoveDegree, int LGs, int SGs)
    if (Serial.available())
    {
       int state = int(Serial.read());
       //q -- HBL
       if(state == 113){
           int steps = moveSteps(hour_large_degree, HOUR_LGEARNUM, HOUR_SGEARNUM);
           move(steps, HOUR_MOTOR1, HOUR_MOTOR2, HOUR_MOTOR3, HOUR_MOTOR4);
       }
       //w -- HBR
       else if(state == 119){
           int steps = moveSteps(hour_large_degree*(-1), HOUR_LGEARNUM, HOUR_SGEARNUM);
           move(steps, HOUR_MOTOR1, HOUR_MOTOR2, HOUR_MOTOR3, HOUR_MOTOR4);
       }
       //e -- HSL
       else if(state == 101){
           int steps = moveSteps(hour_small_degree, HOUR_LGEARNUM, HOUR_SGEARNUM);
           move(steps, HOUR_MOTOR1, HOUR_MOTOR2, HOUR_MOTOR3, HOUR_MOTOR4);
       }
       //r -- HSR
       else if(state == 114){
           int steps = moveSteps(hour_small_degree*(-1), HOUR_LGEARNUM, HOUR_SGEARNUM);
           move(steps, HOUR_MOTOR1, HOUR_MOTOR2, HOUR_MOTOR3, HOUR_MOTOR4);
       }//a -- MBL
       else if(state == 97){
           int steps = moveSteps(minute_large_degree, MIN_LGEARNUM, MIN_SGEARNUM);
           move(steps, MIN_MOTOR1, MIN_MOTOR2, MIN_MOTOR3, MIN_MOTOR4);
       }
       //s -- MBR
       else if(state == 115){
           int steps = moveSteps(minute_large_degree*(-1), MIN_LGEARNUM, MIN_SGEARNUM);
           move(steps, MIN_MOTOR1, MIN_MOTOR2, MIN_MOTOR3, MIN_MOTOR4);
       }
       //d -- MSL
       else if(state == 100){
           int steps = moveSteps(minute_small_degree, MIN_LGEARNUM, MIN_SGEARNUM);
           move(steps, MIN_MOTOR1, MIN_MOTOR2, MIN_MOTOR3, MIN_MOTOR4);
       }
       //f -- MSR
       else if(state == 102){
           int steps = moveSteps(minute_small_degree*(-1), MIN_LGEARNUM, MIN_SGEARNUM);
           move(steps, MIN_MOTOR1, MIN_MOTOR2, MIN_MOTOR3, MIN_MOTOR4);
       }
       //g -- go
       else if(state == 103){
           Serial.println("let's go");
            //Start new threads
            motor1Thread = new Thread("sample", motor1MOVE, &motor1Param);
            motor2Thread = new Thread("sample", motor2MOVE, &motor2Param);
       }

       Serial.println(state);
    }
}

////////////////////////////////////////////////////// Helper Function ///////////////////////////////////////////////////////////





// void go(){
//     Serial.println("let's go");
//     //Start new threads
//     motor1Thread = new Thread("sample", motor1MOVE, &motor1Param);
//     motor2Thread = new Thread("sample", motor2MOVE, &motor2Param);

// }

// int moveSteps(int LmoveDegree, int LGs, int SGs)
// {
//     //how many degree for small gears, for one move of big gear
//     int SmoveDegree = LmoveDegree*(LGs/SGs);
//     //need to have factor of 3*3*5
//     //how many steps needed for those degree
//     int moveSteps = STEPFORCIRCLE*SmoveDegree/360;
//     //in order to make moveSteps to int, (l/s)(degreeEach), need to have factor of 3*3*5
//     return moveSteps;
// }

///////////////////////////////////// Motor Function //////////////////////////////////////////
int move(int steps, int MOTOR1, int MOTOR2, int MOTOR3, int MOTOR4){
  int eachStep = 0;
  if(steps > 0){
    //向上 up
    eachStep = -1;
  }
  if(steps < 0){
    //向下 down
    eachStep = 1;
  }
  int thisStep;
  int i = 0;
  int steps_left = abs(steps);

  while(i < abs(steps)){
    i = i + 1;
    steps_left = steps_left + eachStep;
    thisStep = ( steps_left % 8 ) + 1;
    switch (thisStep) {
      case 1:
      //case 100:
      digitalWrite(MOTOR1, HIGH);
      digitalWrite(MOTOR2, LOW);
      digitalWrite(MOTOR3, LOW);
      digitalWrite(MOTOR4, LOW);
      //Serial.print(500);
      break;
      case 2:
      //case 100*2:
      digitalWrite(MOTOR1, HIGH);
      digitalWrite(MOTOR2, HIGH);
      digitalWrite(MOTOR3, LOW);
      digitalWrite(MOTOR4, LOW);
      //Serial.print(1000);
      break;
      case 3:
      //case 100*3:
      digitalWrite(MOTOR1, LOW);
      digitalWrite(MOTOR2, HIGH);
      digitalWrite(MOTOR3, LOW);
      digitalWrite(MOTOR4, LOW);
      //Serial.print(1500);
      break;
      case 4:
      //case 100*4:
      digitalWrite(MOTOR1, LOW);
      digitalWrite(MOTOR2, HIGH);
      digitalWrite(MOTOR3, HIGH);
      digitalWrite(MOTOR4, LOW);
      //Serial.print(2000);
      break;
      case 5:
      //case 100*5:
      digitalWrite(MOTOR1, LOW);
      digitalWrite(MOTOR2, LOW);
      digitalWrite(MOTOR3, HIGH);
      digitalWrite(MOTOR4, LOW);
      //Serial.print(2500);
      break;
      case 6:
      //case 100*6:
      digitalWrite(MOTOR1, LOW);
      digitalWrite(MOTOR2, LOW);
      digitalWrite(MOTOR3, HIGH);
      digitalWrite(MOTOR4, HIGH);
      //Serial.print(3000);
      break;
      case 7:
      //case 100*7:
      digitalWrite(MOTOR1, LOW);
      digitalWrite(MOTOR2, LOW);
      digitalWrite(MOTOR3, LOW);
      digitalWrite(MOTOR4, HIGH);
      //Serial.print(3500);
      break;
      case 8:
      //case 100*8:
      digitalWrite(MOTOR1, HIGH);
      digitalWrite(MOTOR2, LOW);
      digitalWrite(MOTOR3, LOW);
      digitalWrite(MOTOR4, HIGH);
      //Serial.print(4000);
      break;
    }
    delay(2);
  }
  return 1;
}

///////////////////////////////////// Internet Function //////////////////////////////////////////
void lightHandler(const char *event, const char *data)
{
  lightDataNum++;
  Serial.print(lightDataNum);
  Serial.print(event);
  Serial.print(", data: ");
  Serial.print(data);
  if (data){
    //the range of the light
    lightData = atoi(data) - LIGHT_MIN;
    Serial.print(", after processing: ");
    Serial.print(lightData);
    lightTotal = lightTotal + lightData;
    lightAve = lightTotal/lightDataNum;

    Serial.print(", averageData");
    Serial.println(lightAve);
  }
  else
    Serial.println("NULL");
}

void motionHandler(const char *event, const char *data)
{
    ifMotionNum++;
    // Serial.print(ifMotionNum);
    // Serial.print(event);
    // Serial.print(", motion data: ");
    if (data){
        //the range of the light
        ifMotion = atoi(data)*10 - MOTION_MIN;
        ifMotionTotal = ifMotionTotal + ifMotion;
        ifMotionAvg = ifMotionTotal/ifMotionNum;
        // Serial.print(ifMotion);
        // Serial.print(", averageMotionData");
        // Serial.println(ifMotionAvg);
    }
    else
        Serial.println("NULL");
}

int tempChange(String command) {
    /* Spark.functions always take a string as an argument and return an integer.
    Since we can pass a string, it means that we can give the program commands on how the function should be used.
    In this case, telling the function "on" will turn the LED on and telling it "off" will turn the LED off.
    Then, the function returns a value to us to let us know what happened.
    In this case, it will return 1 for the LEDs turning on, 0 for the LEDs turning off,
    and -1 if we received a totally bogus command that didn't do anything to the LEDs.
    */
    webTempNum++;
    Serial.print("temperature data from the web is coming: ");
    Serial.print(command);

    webTemp = atoi(command) - TEMP_MIN;

    webTempTotal = webTempTotal + webTemp;
    Serial.print(", The total is: ");
    Serial.print(webTempTotal);
    webTempAvg = webTempTotal/webTempNum;
    Serial.print(", The average is: ");
    Serial.println(webTempAvg);
    return 1;
}

//clock adjustment function

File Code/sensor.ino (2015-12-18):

char publishString1[180];
char publishString2[180];
void setup()
{
  Serial.begin(9600);
  pinMode(A1, OUTPUT);
}

void loop()
{
    int lightSensor = analogRead(A2);
    int motionSensor = digitalRead(D2);

    sprintf(publishString1,"%d",lightSensor);
    Serial.println(publishString1);
    Particle.publish("light1991pwpw", publishString1);
    delay(1000);
    sprintf(publishString2,"%d",motionSensor);
    Serial.println(publishString2);
    Particle.publish("motion", publishString2);
    //Serial.println(analogRead(A1));
    delay(1000);
}

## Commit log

2015-12-14 Sunday update #2
    [final-motor_holder.stl, finial.stl]
2015-12-17 Laser cut files update
2015-12-18 cleaning everything up
    Moving the files and folders in a better order, and deleted some
    reference files.
    [final-clock_overview.stl, final-motor_holder.stl, finial.stl]
